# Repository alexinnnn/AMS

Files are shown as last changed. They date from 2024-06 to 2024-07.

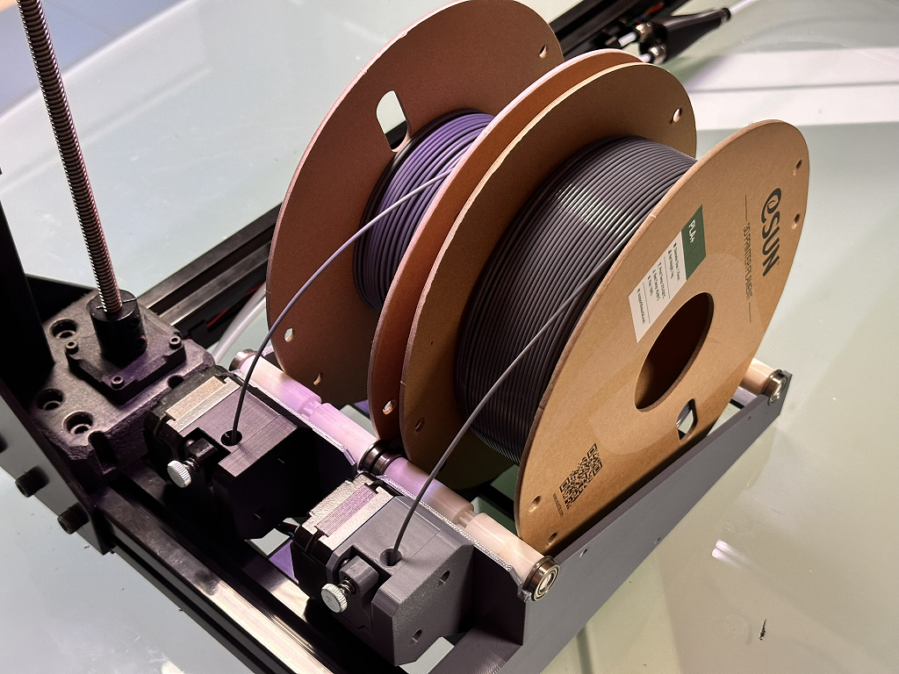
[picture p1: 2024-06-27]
AMS.png

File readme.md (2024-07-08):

AMS - Automatic management system

(обновлено 08.07.2024)

Это система автоматической заправки-выгрузки филамента для 3д принтера. Разрабатывалась исключительно для себя, но так как появился интерес у общественности, решено было выложить для всех.
Для загрузки катушка кладется на ролики, вставляется пластик и по кнопке/макросу LOAD_FILAMENT пластик загружается в голову.
При выгрузке по кнопке/макросу UNLOAD_FILAMENT пластик выгружается обратно до мотора, при этом катушка наматывает обратно пластик.

Работает автозагрузка при старте, автовыгрузка при окончании печати, автозамена при окончании пластика, автозамена при многоцветной печати.

Из электроники система состоит из 2 моторов в фидерах и датчика филамента на голове, ВСЕ.
В ams.step можно посмотреть все устройство.
Крепление на профиль 3030 (RatRig)
Из фидеров трубки приходят в голову через splitter 2-IN-1 (4-IN-1)
Прошивка на основе HappyHare для Klipper. Совместима с последней версией клиппера на 27.06.2024.

Система ERCF не подошла, так как более сложная и катушка не наматывает пластик. Была задача все упростить и за основу взять AMS от BambuLab.
Очень много лишнего и мусора везде, но работает.

Для сборки требуется:

1. Комплект шестеренок, штифтов и пружинки от BMG/клона фидера
2. 2 практически любых шаговых мотора 42х42мм, 2 свободных места на плате управления с драйверами
3. Винты М3, трубки
4. Датчик филамента на голове
5. Размер подшипников для роликов можно посмотреть в step, подходят от Flying Bear Reborn V1 от верхних креплений валов Z, либо переделать на свои.

Установка:

1. Печатаем всю конструкцию из ams.step (или из папки stl), фидер из любого материала кроме PLA, остальное можно и из PLA если не будет в термокамере.
2. Копируем из папки extras в папку extras клиппера 2 файла.
3. Копируем папку config/mmu в папку config клиппера все.

Настройка:

1. В printer.cfg в конец добавить строки:

[include mmu/\*.cfg]

[include mmu/base/\*.cfg]

2. В mmu/base/mmu_hardware.cfg настроить секции stepper_mmu_gear (и tmc2209 stepper_mmu_gear), stepper_mmu_selector (b tmc2209 stepper_mmu_selector) для моторов
3. Проверить в вашем конфиге секцию filament_switch_sensor для датчика филамента на голове. Она должна называться [filament_switch_sensor extruder_sensor].
4. В mmu/filament_management.cfg в секции [gcode_macro LOAD_FILAMENT] внести variable_length1 и variable_length2 - это расстояние для выгрузки филамента от датчика до 2-3 см недоезжая до шестеренок мотора, можно настроить в процессе работы. Координаты в командах G0 X475 ИЗМЕНИТЬ НА СВОИ!!! Это координаты движения головы через прочистку после заправки пластика.
5. В mmu/macros.cfg в секции [gcode_macro _POWER_OFF_PRINTER] изменить имя устройства "printer" на ваше, это макрос для автовыключения принтера (если это необходимо).
6. В mmu/print_management.cfg проверить все макросы, особенно [START_PRINT] и [END_PRINT]. ИЗМЕНИТЬ КООРДИНАТЫ ПАРКОВКИ ОКОЛО ПРОЧИСТКИ X490 Y497 НА ВАШИ!!!

Выбор пластика происходит перед стартом печати с помощью команд T1 или T2, а также стандартные кнопки T1 и T2, которые появятся в интерфейсе Mainsail. Если пластик заканчивается в процессе печати, загружается следующий из соседней катушки.

Стартовый g-code в слайсере (OrcaSlicer):  
START_PRINT EXTRUDER_TEMP=[nozzle_temperature_initial_layer] BED_TEMP=[bed_temperature_initial_layer_single]

Конечный g-code в слайсере:  
END_PRINT

g-code, выполняемый при смене прутка, для многоцветной печати (OrcaSlicer):  
PARK  
UNLOAD_FILAMENT T=0  
T{next_extruder+1}  
LOAD_FILAMENT T={new_filament_temp} MOVECLEARAFTER=1  
RESTORE_GCODE_STATE name=PARK_STATE MOVE=1 MOVE_SPEED=700  

Вроде все. Мог что-то забыть.

PS Вся эта сборка предоставляется AS IS (КАК ЕСТЬ). ПОЛНОСТЬЮ под вашу ответственность и тд и тп.

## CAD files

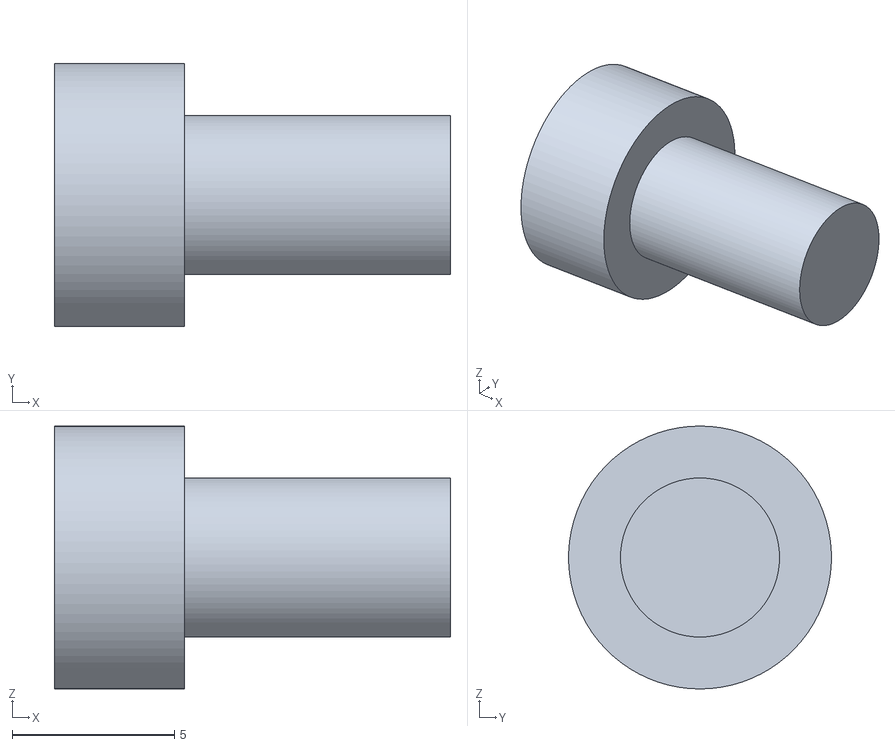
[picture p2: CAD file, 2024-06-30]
stl/NewGear1Pin.STL
12.2 x 8.09 x 8.10

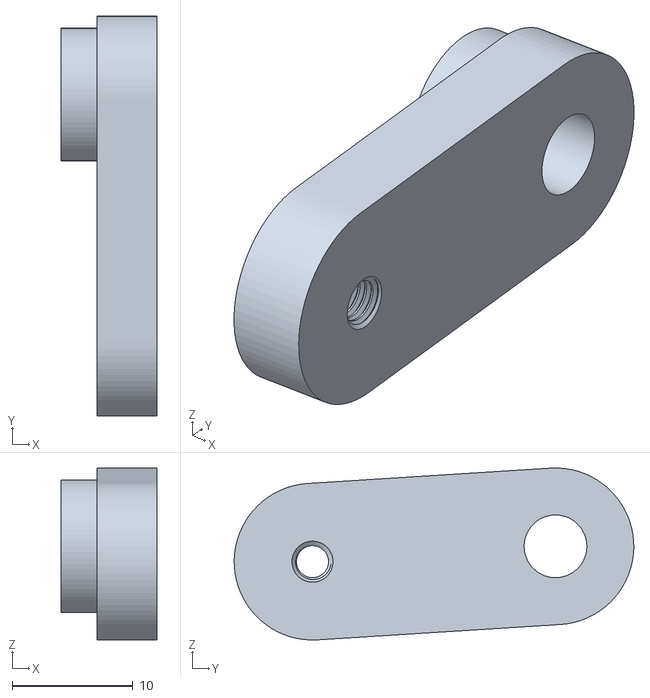
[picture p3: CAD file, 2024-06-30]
stl/GearSup2.STL
8.00 x 33.2 x 14.3

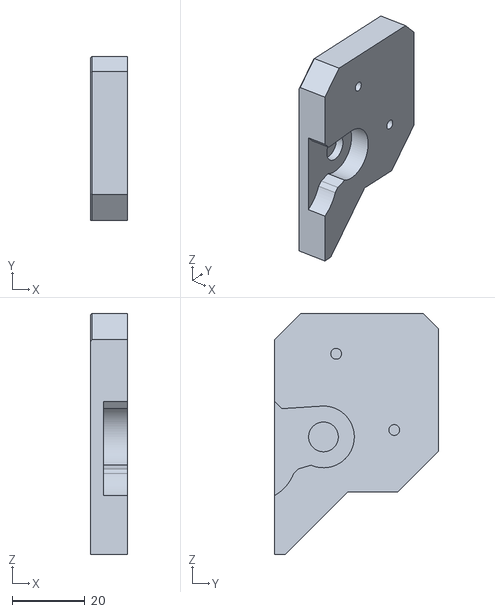
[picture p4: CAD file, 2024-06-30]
stl/MotorCap.STL
10.2 x 45.2 x 66.4

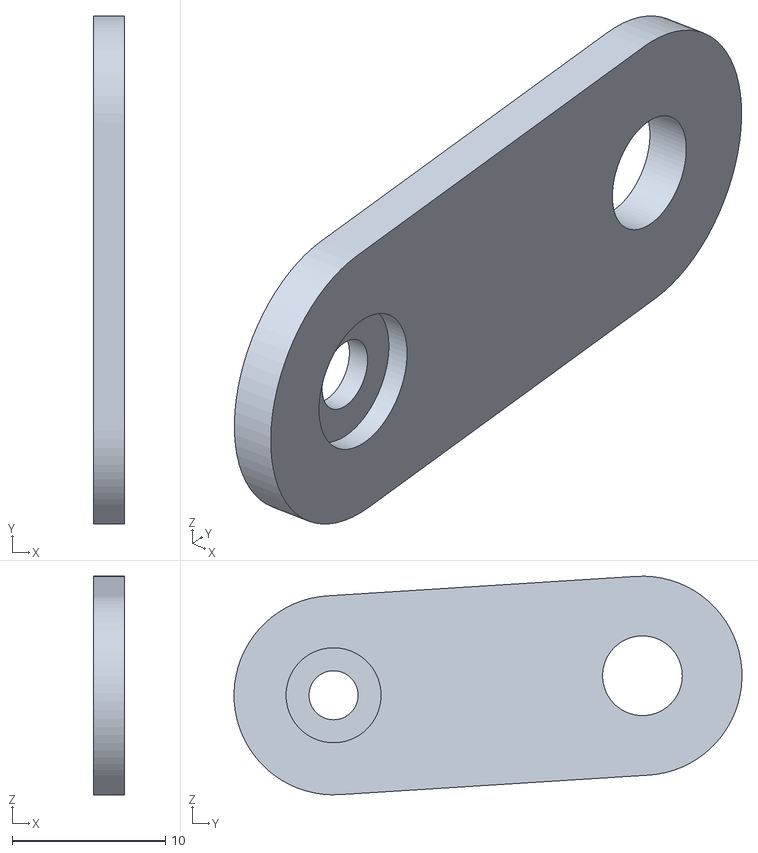
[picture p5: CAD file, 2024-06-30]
stl/GearSup1.STL
2.00 x 33.2 x 14.3

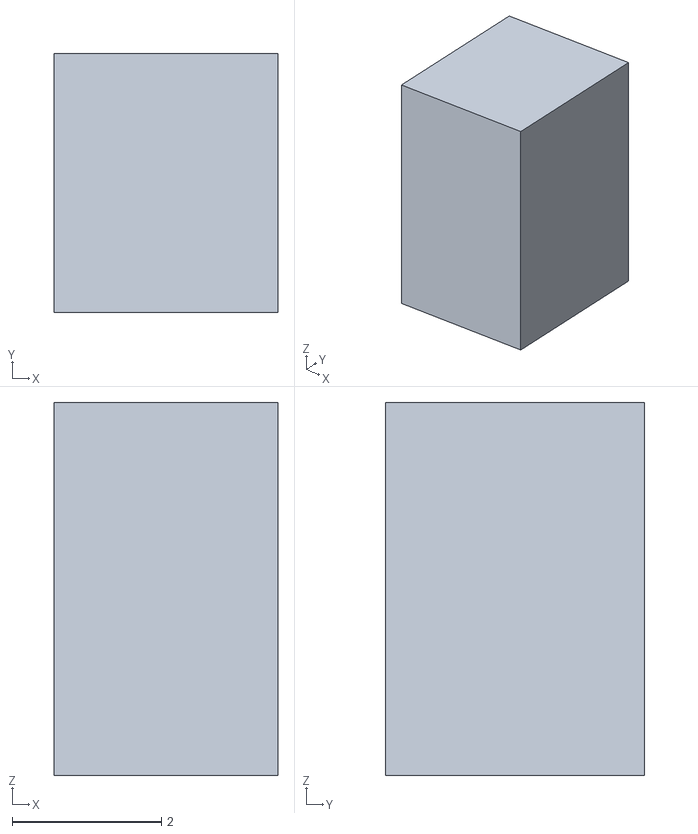
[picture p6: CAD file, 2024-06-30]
stl/GearPin.STL
3.00 x 3.47 x 5.00

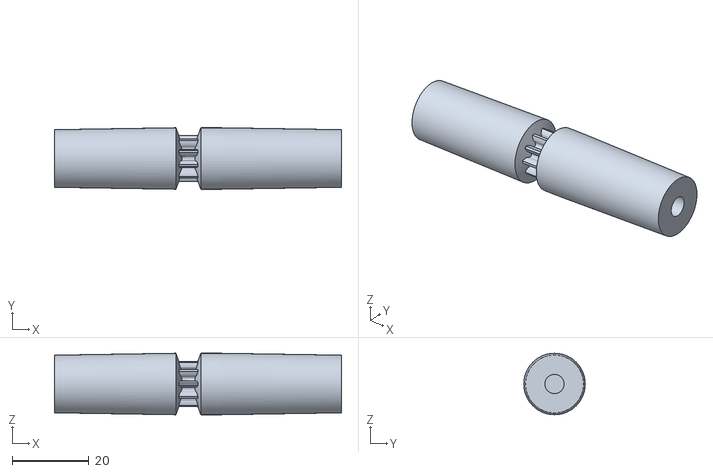
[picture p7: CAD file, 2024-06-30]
stl/FrontRoller.STL
74.6 x 16.0 x 16.0

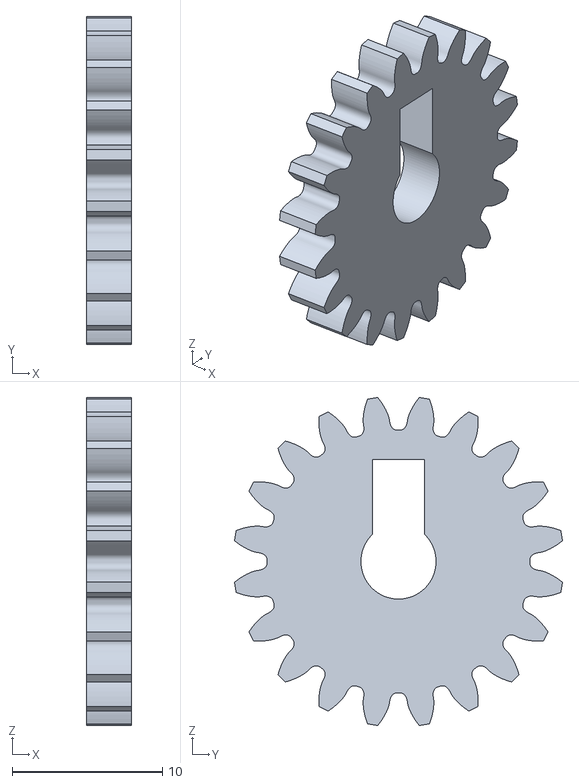
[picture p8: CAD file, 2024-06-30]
stl/NewGear1.STL
3.00 x 21.8 x 21.8

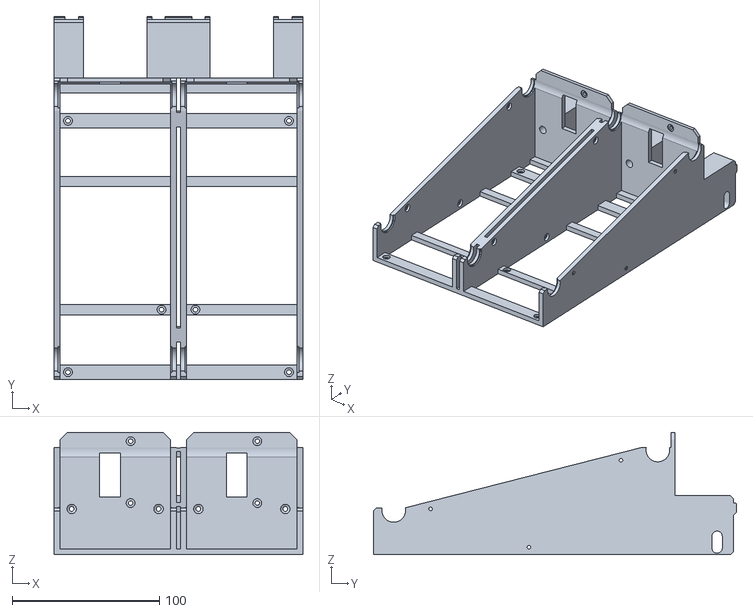
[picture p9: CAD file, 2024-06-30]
stl/BigBase.STL
169.0 x 246.5 x 83.0

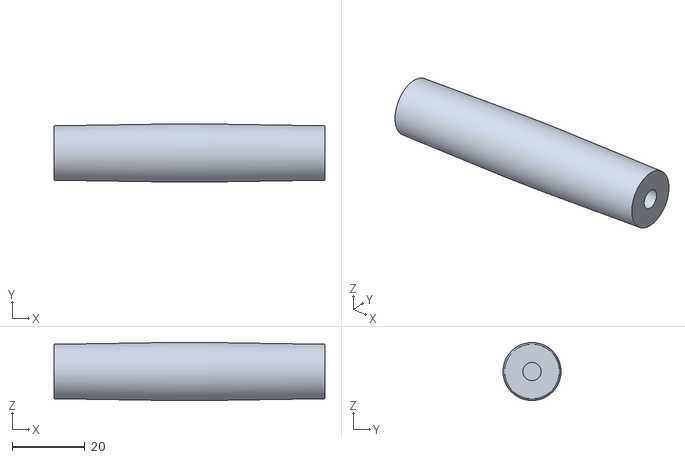
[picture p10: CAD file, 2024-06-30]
stl/BackRoller.STL
74.6 x 16.0 x 16.0

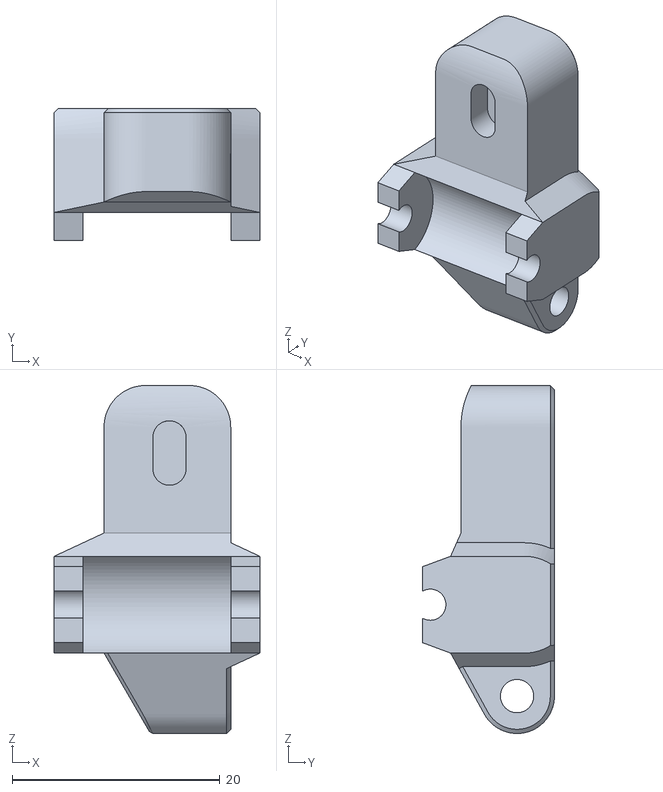
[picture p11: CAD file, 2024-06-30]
stl/Lapk.STL
19.8 x 12.7 x 33.5

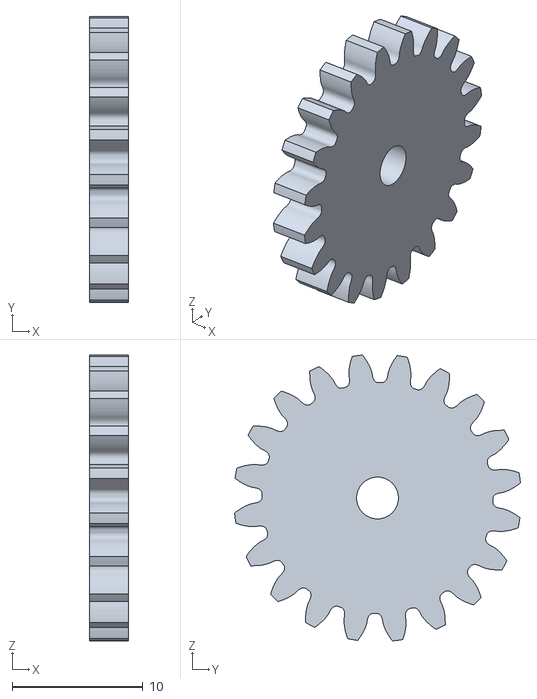
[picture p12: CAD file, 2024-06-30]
stl/NewGear2.STL
3.00 x 21.9 x 21.9

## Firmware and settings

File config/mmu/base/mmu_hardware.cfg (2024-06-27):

## Happy Hare MMU hardware config file with config for unknown
##
## Common external mcus:
## 1) EASY-BRD
##  J6 Jumper setting
##   Option 1: Pins 2-3 and 4-5, i.e.  .[..][..] (recommended)
##   This allows for option of "touch" selector setup. Note that this enables the option disables the "extra"
##   switch so the toolhead sensor (if used) would have to be connected to the main mcu
##
##   Option 2: Pins 1-2 and 4-5, i.e.  [..].[..]
##   It you don't care about selector touch operation. The "extra" switch is enabled for other uses
##
##  Note that the EASY-BRD does not expose the DIAG pin for the gear stepper
##
## 2) Fysetc Burrows ERB
##  No jumper configuration is required for Fysetc Burrows ERB board. Both Selector and Gear DIAG pins are exposed
##
##  ERB firmware flashing notes:
##   Must have 12v/24v supply connected
##    > make menuconfig (rpi2040, No bootloader)
##    > make
##  Put card in boot loader mode: Press & Hold 'BOOTSEL' ; click 'RST; ; Release 'BOOTSEL'
##    > make flash FLASH_DEVICE=2e8a:0003
##
## ------
##
## Note about "touch" endstops: Happy Hare provides extremely flexible homing options using both single steppers or synced steppers.
## The "touch" option leverages stallguard and thus requires the appropriate 'diag_pin' and stallguard parameters set on the TMC driver
## section.  If you have the diag_pin exposed, it is harmless to define this because they will only be used when explicitly needed
## and configured.
##
## Touch option for each stepper provides these benefits / possibilities (experimental):
##  - on extruder stepper allows for the automatic detection of the nozzle!
##  - on selector stepper allows for the automatic detection of filament stuck in the gate and subsequent recovery
##  - on gear stepper allows for the automatic detection of the extruder entrance
##
## These sound wonderful right?  They are, but there are caveats:
##  - The external EASY-BRD and ERB mcu's are terrible at detecting stallguard and often result in an "undervoltage error". It is generally
##    possible to get selector touch (TMC2209) tuned especially if you set 'stealthchop_threshold' to a value greater than homing speeds and
##    less than move speed. I.e. the stepper runs in stealthchop mode when homing. [klipper experts will know that it switches the chip mode
##    automatically to stealthchop and then back for Stallguard2 support, howver the automatic switching back to spreadcycle at the end homing
##    move seems to provoke the error condition and setting 'shealthchip_threshold' appropriately avoids this condition. More than you wanted
##    to know I'm sure!
##  - I have not had much luck with touch (stallguard) on the gear stepper with EASY-BRD and ERB mcu's and you really want the extra torque
##    of spreadcycle so adjusting 'stealthchop_threshold' is not really an option
##  - Enabling on the extruder stepper is viable but you will likley have to change jumpers on your main mcu to expose the DIAG pin for
##    whichever driver the extruder stepper is connected to.
##
## In summary, "touch" homing with your MMU is an advanced option that requires patience and careful tuning.  Luckily everything works with
## regular endstops and there are workaround options for certain homing points (like extruder entry) in the absence of any endstop.
## I'm really interested in creative setups that you come up with. Ping me on Discord (moggieuk#6538)
##
##
## See mmu.cfg for serial definition and pins aliaes
##


# HOMING CAPABLE EXTRUDER (VERY ADVANCED) ----------------------------------------------------------------------------------
# With Happy Hare installed the extruder can be homed.  You will find the usual 'endstop' parameters can be added to your
# '[extruder]' section.  Useless you have some clever load cell attached to your nozzle it only really makes sense to configure 
# stallguard style "touch" homing. To do this add lines similar to this to your existing '[extruder]' definition whether
# you have it defined in printer.cfg.
#
#    [extruder]
#    endstop_pin: tmc2209_extruder:virtual_endstop
#
# Also be sure to add the appropriate stallguard config to the TMC section, e.g.
#
#    [tmc2209 extruder]
#    diag_pin: E_DIAG			# Set to MCU pin connected to TMC DIAG pin for extruder
#    driver_SGTHRS: 100			# 255 is most sensitive value, 0 is least sensitive
#
# Happy Hare will take care of the rest and add a 'mmu_ext_touch' endstop automatically


# FILAMENT DRIVE GEAR STEPPER  ---------------------------------------------------------------------------------------------
# Note that 'toolhead' & `mmu_gear` endstops will automatically be added if a toolhead sensor or gate sensor is defined
#
# The default values are tested with the ERCF BOM NEMA14 motor. Please adapt these values to the motor you are using
# Example : for NEMA17 motors, you'll usually use higher current
#

#[tmc2209 stepper_mmu_gear]
#uart_pin: mmu:MMU_GEAR_UART
##uart_address: 0 			# Comment out for ERB board
#interpolate: True
#run_current: 0.5			# ERCF BOM NEMA14 motor
#hold_current: 0.1			# Recommend to be small if not using "touch" or move (TMC stallguard)
#sense_resistor: 0.110			# Usually 0.11, 0.15 for BTT TMC2226
#stealthchop_threshold: 0		# Spreadcycle has more torque and better at speed

#
# Uncomment two lines below if you have TMC and want the ability to use filament "touch" homing with gear stepper
#diag_pin: ^mmu:MMU_GEAR_DIAG		# Set to MCU pin connected to TMC DIAG pin for gear stepper
#driver_SGTHRS: 60			# 255 is most sensitive value, 0 is least sensitive

[stepper_mmu_gear]
#rotation_distance: 22.7316868		# Bondtech 5mm Drive Gears. Will be overriden by `mmu_gear_rotation_distance` in mmu_vars.cfg
gear_ratio: 1:1			# ERCF 80:20, Tradrack 50:17
#full_steps_per_rotation: 200		# 200 for 1.8 degree, 400 for 0.9 degree
step_pin: PF9
dir_pin: PF10
enable_pin: !PG2
rotation_distance: 23 # less is faster
microsteps: 16

[tmc2209 stepper_mmu_gear]
uart_pin: PF2
#tx_pin: mmu:PC10
#uart_address: 2
run_current: 0.800
hold_current: 0.100
#stealthchop_threshold: 999999
interpolate: False
#driver_SGTHRS: 50
#diag_pin: mmu:PC1
#driver_SGT: -64  # -64 is most sensitive value, 63 is least sensitive

#
# Uncomment the two lines below to enable filament "touch" homing option with gear motor
#extra_endstop_pins: tmc2209_stepper_mmu_gear:virtual_endstop
#extra_endstop_names: mmu_gear_touch


# SELECTOR STEPPER  --------------------------------------------------------------------------------------------------------
# Consult doc if you want to setup selector for "touch" homing instead or physical endstop
#
#[tmc2209 stepper_mmu_selector]
#uart_pin: mmu:MMU_SEL_UART
##uart_address: 1 			# Comment out for ERB board
#run_current: 0.4			# ERCF BOM NEMA17 motor
#hold_current: 0.2			# Can be small if not using "touch" movement (TMC stallguard)
#interpolate: True
#sense_resistor: 0.110
#stealthchop_threshold: 100		# Stallguard "touch" movement (slower speeds) best done with stealthchop

#
# Uncomment two lines below if you have TMC and want to use selector "touch" movement
#diag_pin: ^mmu:MMU_SEL_DIAG 		# Set to MCU pin connected to TMC DIAG pin for selector stepper
#driver_SGTHRS: 75			# 255 is most sensitive value, 0 is least sensitive

[stepper_mmu_selector]
#step_pin: mmu:MMU_SEL_STEP
#dir_pin: !mmu:MMU_SEL_DIR
#enable_pin: !mmu:MMU_SEL_ENABLE
#rotation_distance: 40
#microsteps: 16 				# Don't need high fidelity
#full_steps_per_rotation: 200		# 200 for 1.8 degree, 400 for 0.9 degree
#endstop_pin: ^mmu:MMU_SEL_ENDSTOP	# Selector microswitch
#endstop_name: mmu_sel_home
step_pin: PG4
dir_pin: PC1
enable_pin: !PA2
rotation_distance: 23 # # less is faster
microsteps: 16

[tmc2209 stepper_mmu_selector]
uart_pin: PC7
#tx_pin: mmu:PC10
#uart_address: 0
run_current: 0.800
hold_current: 0.100
#stealthchop_threshold: 999999
interpolate: False
#driver_SGTHRS: 50
#diag_pin: mmu:PC0
#driver_SGTHRS: 255  # 255 is most sensitive value, 0 is least sensitive tmc2209
#driver_SGT: -64  # -64 is most sensitive value, 63 is least sensitive

#
# Uncomment two lines below to give option of  selector "touch" movement
#extra_endstop_pins: tmc2209_stepper_mmu_selector:virtual_endstop
#extra_endstop_names: mmu_sel_touch


# SELECTOR SERVO -----------------------------------------------------------------------------------------------------------
# Basic servo PWM setup. If these values are changed then the angles defined for different positions will also change
#
#[mmu_servo mmu_servo]
#pin: mmu:PB0 # MMU_SERVO
#maximum_servo_angle: 180
#minimum_pulse_width: 0.00085
#maximum_pulse_width: 0.00215
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

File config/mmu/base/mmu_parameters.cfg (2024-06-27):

###########################################################################
# Happy Hare main configuration parameters
#
# Note that macro configuration is specifed separately in:
#   mmu_sequence.cfg - Customization of loading and unloading sequences
#   mmu_form_tip.cfg - Tuning of standalone tip forming
#   mmu_cut_tip.cfg  - Tuning of toolhead based tip cutting
# Full details in https://github.com/moggieuk/Happy-Hare/tree/main/doc/configuration.md
#
[mmu]
happy_hare_version: 2.42	# Don't mess, used for upgrade detection
#
# The vendor and version config is important to define the capabilities of the MMU and basic CAD dimensions. These can
# all be overridden with the `cad` parameters detailed in the documentation but the vendor setting saves time.
#
# ERCF
# 1.1 original design, add "s" suffix for Sprigy, "b" for Binky, "t" for Triple-Decky
#     e.g. "1.1sb" for v1.1 with Springy mod and Binky encoder
#
# 2.0 new community ERCFv2, add "h" suffix for ThumperBlocks
#
# Tradrack
# 1.0 add "e" if using encoder is fitted
#
# Prusa
#  - Comming soon (use Other for now)
#
# Other
#  - Generic setup that will require further customization of `cad` parameters. See doc and section at the end
#
mmu_vendor: Other			# MMU family
mmu_version: 1			# MMU hardware version number (add mod suffix documented above)
mmu_num_gates: 2 			# Number of selector gates


# MMU Limits ---------------------------------------------------------------------------------------------------------------
#
# Define the physical limits of your MMU. These setings will be respected regardless of individual speed settings.
#
gear_max_velocity: 300			# Never to be exceeded gear velocity regardless of specific parameters
gear_max_accel: 500			# Never to be exceeded gear accelaration regardless of specific parameters
selector_max_velocity: 250		# Never to be exceeded selector velocity regardless of specific parameters
selector_max_accel: 100		# Never to be exceeded selector accelaration regardless of specific parameters


# Servo configuration  -----------------------------------------------------------------------------------------------------
#
# Angle of the servo in three named positions
#   up   = tool is selected and filament is allowed to freely move through gate
#   down = to grip filament
#   move = ready the servo for selector move (optional - defaults to up)
# V2.4 on: These positions are only for initial config they are replaced with calibrated servo positions in `mmu_vars.cfg`
#
# Note that leaving the servo active when down can stress the electronics and is not recommended with EASY-BRD or ERB board
# unless the 5v power supply has been improved and it is not necessary with standard ERCF builds
# Make sure your hardware is suitable for the job!
#
servo_up_angle: 0			# ERCF: MG90S: 30  ; SAVOX SH0255MG: 140 ; Tradrack: 145
servo_down_angle: 0			# ERCF: MG90S: 140 ; SAVOX SH0255MG: 30  ; Tradrack: 1
servo_move_angle: 0			# Optional angle used when selector is moved (defaults to up position)
servo_duration: 0.2			# Duration of PWM burst sent to servo (automatically turns off)
servo_dwell: 0.5			# Minimum time given to servo to complete movement prior to next move
servo_active_down: 0			# CAUTION: 1=Force servo to stay active when down, 0=Release after movement
#servo_buzz_gear_on_down: 3		# Whether to "buzz" the gear stepper on down to aid engagement


# Logging ------------------------------------------------------------------------------------------------------------------
#
# log_level & logfile_level can be set to one of (0 = essential, 1 = info, 2 = debug, 3 = trace, 4 = stepper moves)
# Generally you can keep console logging to a minimal whilst still sending debug output to the mmu.log file
# Increasing the console log level is only really useful during initial setup to save having to constantly open the log file
#
log_level: 1
log_file_level: 3			# Can also be set to -1 to disable log file completely
log_statistics: 1 			# 1 to log statistics on every toolchange (default), 0 to disable (but still recorded)
log_visual: 2				# 1 log visual representation of filament, 0 = disable
log_startup_status: 1			# Whether to log tool to gate status on startup, 1 = summary (default), 2 = full, 0 = disable
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

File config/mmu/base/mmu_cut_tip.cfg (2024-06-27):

###########################################################################
# Happy Hare supporting macros
#   Standalone Tip Cutting for "Filametrix" style toolhead cutters
#
# To configure, set
#   'form_tip_macro: _MMU_CUT_TIP' in 'mmu_parameters.cfg'
#
# Default configuration is good for Stealthburner with CW2 and Voron Revo nozzle
#
# IMPORTANT:
#   The park position of the filament is relative to the nozzle and
#   represents where the end of the filament is after cutting. The park position
#   is important and used by Happy Hare both to finish unloading the extruder
#   as well as to calculate how far to advance the filament on the subsequent load.
#
# When using this macro it is important to turn off tip forming in your slicer and
# force Happy Hare to always run this when loading filament by adding:
#   'force_form_tip_standalone: 1' in 'mmu_parameters.cfg'
# Also decide on 'return_to_wipetower' (here) vs 'enable_park' (mmu_sequence.cfg)
#
# Implementation note: It is important to report back the position the cutter
# leaves the filament in the extruder via the variable 'output_park_pos' so this
# is set dynamically in gcode with this construct:
#   SET_GCODE_VARIABLE MACRO=_MMU_CUT_TIP VARIABLE=output_park_pos VALUE=..
#
[gcode_macro _MMU_CUT_TIP]
description: Cut filament by pressing the cutter on a pin with a horizontal movement

# By default this macro will return toolhead to initial position (usually wipetower) after the cut is complete.
# If using parking logic you may want to disable this and set 'park_after_form_tip:1' in mmu_sequence.cfg
variable_restore_position: 1		# 1 = return to initial position after cut, 0 = don't return

# Distance from the internal nozzle tip to the cutting blade. This dimension is based on your
# toolhead and should not be used for tuning.
variable_blade_pos: 37.5

# Distance to retract prior to making the cut, this reduces wasted filament (left behind in extruder)
# but might cause clog if set too large and/or if there are gaps in the hotend assembly 
# This must be less than 'blade_pos', 5mm less is a good starting point
variable_retract_length: 32.5

# This should be the position of the toolhead where the cutter arm just lightly touches the pin
variable_pin_loc_x: 14			# Location of depressor pin. Must set
variable_pin_loc_y: 250			# Location of depressor pin. Must set

# This distance is added to 'pin_loc_x' to determine the starting position and to create a small saftely
# distance that aids in generating momentum
variable_pin_park_x_dist: 5.0

# Position of the toolhead when the cutter is fully compressed
# Should leave a small headroom (should be a bit larger than 0, or whatever xmin is) to avoid banging the toolhead or gantry
variable_pin_loc_x_compressed: 0.5

# Retract length and speed after the cut so that the cutter blade doesn't get stuck on return to origin position
variable_rip_length: 1			# Distance to retract to aid lever decompression (>= 0)
variable_rip_speed: 12			# mm/s

# Pushback of the remaining tip from the cold end into the hotend. This does not have to push back all the way, just
# sufficient to ensure filament fragment stays in hot end. Cannot be larger than 'retract_length'
variable_pushback_length: 5
variable_pushback_dwell_time: 0		# Time to dwell after the pushback

# Speed related settings
# Note that if the cut speed is too fast, the steppers can lose steps. Therefore, for a cut: 
# - We first make a fast move to accumulate some momentum and get the cut blade to the initial contact with the filament
# - We then make a slow move for the actual cut to happen 
variable_travel_speed: 166		# mm/s
variable_cut_fast_move_speed: 33	# mm/s
variable_cut_slow_move_speed: 8		# mm/s
variable_evacuate_speed: 166		# mm/s
variable_cut_dwell_time: 50		# Time to dwell at the cut point in ms
variable_cut_fast_move_fraction: 1.0	# Fraction of the move that uses fast move 

variable_extruder_move_speed: 1500	# mm/s for all extruder movement

# Safety margin for fast vs slow travel
# When traveling to the pin location, we make a safer but longer move if we are closer to the pin than this specified margin
# Usually setting these to the size of the toolhead (plus a small margin) should be good enough 
variable_safe_margin_x: 30
variable_safe_margin_y: 30

# If gantry servo option is installed, enable the servo and set up and down angle positions
variable_gantry_servo_enabled: 0	# 1 = enabled, 0 = disabled
variable_gantry_servo_down_angle: 55
variable_gantry_servo_up_angle: 180

# -------------------------- Internal Don't Touch -------------------------
variable_final_eject: 0			# MMU_TEST_FORM_TIP testing only: Whether to eject the filament at the end
variable_output_park_pos: 0		# Dynamically set in macro

gcode:
    {% set RETRACT_LENGTH = params.RETRACT_LENGTH | default(printer['gcode_macro _MMU_CUT_TIP']['retract_length']) | float %}
    {% set PUSHBACK_LENGTH = params.PUSHBACK_LENGTH | default(printer['gcode_macro _MMU_CUT_TIP']['pushback_length']) | float %}
    {% set FINAL_EJECT = params.FINAL_EJECT | default(printer['gcode_macro _MMU_CUT_TIP']['final_eject']) | int %}

    SAVE_GCODE_STATE NAME=_MMU_CUT_TIP_state

    {% if ("xy" not in printer.toolhead.homed_axes) %}
        G28 X Y
    {% endif %}

    SET_PRESSURE_ADVANCE ADVANCE=0 # Temporarily disable pressure advance. Happy Hare will restore it

    {% set pin_park_x_loc = pin_loc_x + pin_park_x_dist %}
    {% set pin_park_y_loc = pin_loc_y %}

    G90 # Absolute positioning
    M83 # Relative extrusion
    G92 E0
    {% if RETRACT_LENGTH > 0 %}
        # Retract to save filament waste, repeat to allow some cooling
        G1 E-{RETRACT_LENGTH} F{extruder_move_speed|float * 60}
        G1 E{RETRACT_LENGTH / 2} F{extruder_move_speed|float * 60} 
        G1 E-{RETRACT_LENGTH / 2} F{extruder_move_speed|float * 60}
    {% endif %}

    _FILAMETRIX_GANTRY_SERVO_UP
    _FILAMETRIX_MOVE_TO_CUTTER_PIN PIN_PARK_X_LOC={pin_park_x_loc} PIN_PARK_Y_LOC={pin_park_y_loc}
    _FILAMETRIX_GANTRY_SERVO_DOWN
    _FILAMETRIX_DO_CUT_MOTION PIN_PARK_X_LOC={pin_park_x_loc} RIP_LENGTH={rip_length}
    _FILAMETRIX_GANTRY_SERVO_UP

    # Optionally pushback of the tip residual into the hotend to avoid future catching
    {% if PUSHBACK_LENGTH > 0 %} 
        G1 E{PUSHBACK_LENGTH} F{extruder_move_speed|float * 60} 
        G4 P{pushback_dwell_time}
        G1 E-{PUSHBACK_LENGTH} F{extruder_move_speed|float * 60}
    {% endif %}
    
    # Final eject is for testing
    {% if FINAL_EJECT == 1 %}
        G1 E-80 F{extruder_move_speed|float * 60}
    {% endif %}

    # Dynamically set the required output variables for Happy Hare
    {% set park_pos = blade_pos + rip_length %}
    SET_GCODE_VARIABLE MACRO=_MMU_CUT_TIP VARIABLE=output_park_pos VALUE={park_pos}

    # Restore state and optionally position (usually on wipetower)
    RESTORE_GCODE_STATE NAME=_MMU_CUT_TIP_state MOVE={restore_position} MOVE_SPEED={travel_speed}


###########################################################################
# Helper macro for tip cutting
#
[gcode_macro _FILAMETRIX_MOVE_TO_CUTTER_PIN]
description: Helper to move the toolhead to the target pin in either safe or faster way, depending on toolhead clearance
gcode:
    {% set safe_margin_x = printer['gcode_macro _MMU_CUT_TIP']['safe_margin_x'] | float %}
    {% set safe_margin_y = printer['gcode_macro _MMU_CUT_TIP']['safe_margin_y'] | float %}
    {% set travel_speed = printer['gcode_macro _MMU_CUT_TIP']['travel_speed'] | float %}
    {% set pin_park_x_loc = params.PIN_PARK_X_LOC | float %}
    {% set pin_park_y_loc = params.PIN_PARK_Y_LOC | float %}

    {% if ((printer.gcode_move.gcode_position.x - pin_park_x_loc) | abs < safe_margin_x) or ((printer.gcode_move.gcode_position.y - pin_park_y_loc | float) | abs < safe_margin_y) %}
        # Make a safe but slower travel move
        G1 X{pin_park_x_loc} F{travel_speed|float * 60}
        G1 Y{pin_park_y_loc} F{travel_speed|float * 60}
    {% else %}
        G1 X{pin_park_x_loc} Y{pin_park_y_loc} F{travel_speed|float * 60}
    {% endif %}
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

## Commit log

2024-06-27 Прошивка
    [filament_management.cfg, macros.cfg, mmu.cfg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]
2024-06-27 Описание
2024-06-27 Фото
2024-06-28 ЛИЦЕНЗИЯ
2024-06-28 Обновление
    [filament_management.cfg, print_management.cfg]
2024-06-30 'Описание'
2024-07-08 «Обновление»
    [mmu.cfg]
